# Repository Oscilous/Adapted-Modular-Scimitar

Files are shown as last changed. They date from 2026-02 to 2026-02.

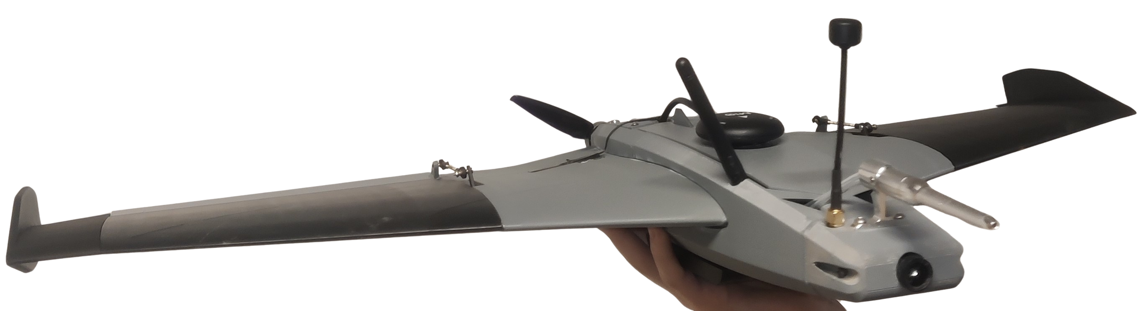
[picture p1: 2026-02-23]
Media/Assembly/4.png

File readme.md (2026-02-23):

# Adapted Modular Scimitar with Payload Mounting Grid

Repository of the HardwareX paper "Field-tested workflow for adapting open-source 3D-printed fixed-wing UAVs for modular payload integration" developed at University of Southern Denmark.



## Abstract

Fixed-wing unmanned aerial vehicles (UAVs) are widely used in environmental monitoring and research, yet sys-
tematic and reproducible methods for integrating arbitrary payloads while preserving aerodynamic performance
remain limited. This work presents a complete hardware workflow for adapting an open-source fixed-wing air-
frame into a modular sensing platform with validated payload integration. The approach combines mechanical
redesign, mass and center of gravity verification, computational fluid dynamics (CFD) aerodynamic assess-
ment, and field validation. The workflow is demonstrated on a sub-1.5 kg 3D-printed Scimitar V2 modified to
be equipped with a reconfigurable payload mounting grid that enables rapid sensor interchange. CFD-guided
design iteration increased aerodynamic efficiency by raising the lift-to-drag ratio from approximately 3.6–5.1
to 8.8–18.2, providing quantitative pre-fabrication screening indicating improved aerodynamic efficiency. Field
testing at RC Parken (Aabenraa, Denmark) in December 2025 validated the sensor logging pipeline by cross-
comparing barometric pressure and demonstrated in-flight temperature and humidity acquisition.

## Directory Structure

```
├── readme.md                    # This file
├── 3D_Printing/                 # 3D printable components
│   ├── 019_Canopy_handle.3mf
│   └── TPU/                     # Flexible TPU parts
│       └── 015_Hinges_TPU.3mf
├── CAD/                         # Complete CAD models (STEP format)
│   ├── Fuselage sections (001-007)
│   ├── Wing designs (008-013)
│   ├── Control surfaces (014-016)
│   ├── Canopy (017, 019)
│   ├── Sensor and component models (018, 020-035)
│   └── [35 STEP files total]
├── CFD/                         # Aerodynamic analysis files
│   ├── project_results.xml
│   ├── Internal_M5GO.*          # Simulation results
│   └── r_000000.fld             # Field data
├── M5 Software/                 # M5Stack firmware
│   └── Drone_Air_Quality_Code.m5f2
├── PX4 Firmware/                # Autopilot configuration
│   ├── Parameters.params        # Pre-tuned parameters
│   └── readme.txt
└── Media/                       # Assembly documentation
    └── Assembly/
```

## License

This project is released under CC BY 4.0.

For questions, contributions, or feedback, please refer to the project repository or contact the team.

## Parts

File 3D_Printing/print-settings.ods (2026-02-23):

For print orientation please navigate to docs/gallery/printing-orientation/
 | Scimitar 2
Part | Profile | Infill % | Time (P1P) | Grams | Modifiers
Wing L 1 | A | 4 gyro | 02:14 | 50 | +support
Wing R 1 | A | 4 gyro | 02:14 | 50 | +support
Wing L 2 | A | 4 gyro | 03:24 | 49 | +support
Wing R 2 | A | 4 gyro | 03:24 | 49 | +support
Wing L 3 | B LW | 8 gyro | 01:09 | 16
Wing R 3 | B LW | 8 gyro | 01:09 | 16
Wing L aileron | A | 8 gyro | 01:25 | 9 | 15 bottom layers
Wing R aileron | A | 8 gyro | 01:25 | 9 | 15 bottom layers
Fuselage 1 | C | 0 | 00:38 | 14
Fuselage 2 | C | 100 | 00:09 | 4
Fuselage 3 | A | 8 gyro | 03:07 | 43 | 10 bottom layers
Fuselage 4 | A | 8 gyro | 02:12 | 32
Fuselage 5 | C | 0 | 00:23 | 8
Batterie plate | C | 10 gyro | 00:20 | 12 | 3 bottom, 3 top
Canopy | C | 8 gyro | 00:28 | 14 | 2 bottom, 2 top
Canopy handle | B | 100 | 00:05 | 1
Motor mount | C | 100 | 00:24 | 6
Wing lock L+R | C | 100 | 00:31 | 15
Hinges (TPU) | B | 100 | 00:10 | 1
 | Total : |  | 24:51 | 398
Profile | Layer hei. | Walls | Top, bottom
A | 0,20 | 1 | 3 | PLA+
B | 0,20 | 2 | 4
C | 0,20 | 3 | 5
A LW | 0,2 | 1 | 3 | Esun / 3DLP Foaming PLA-LW 250°C flow 0.50
B LW | 0,2 | 2 | 4
C LW | 0,2 | 3 | 5

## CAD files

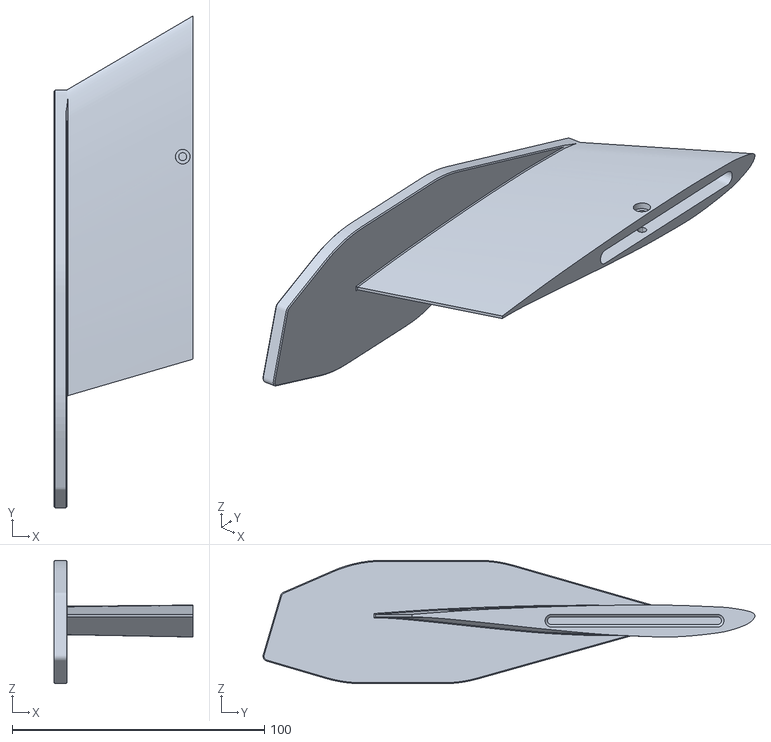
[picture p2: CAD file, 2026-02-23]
3D_Printing/LWPLA/013_Wing_3_Right.STL
55.0 x 195.2 x 49.0

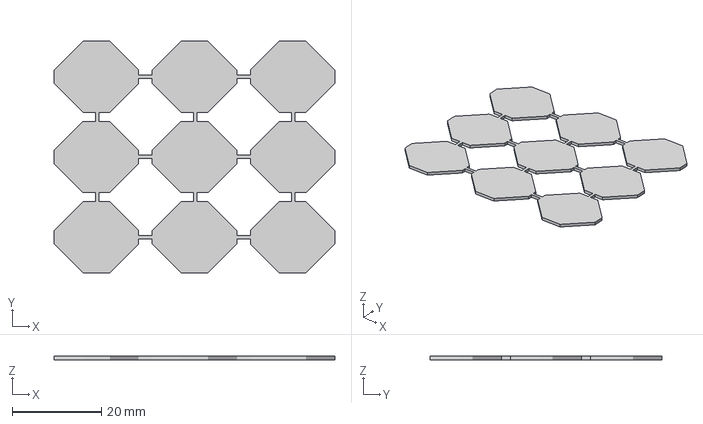
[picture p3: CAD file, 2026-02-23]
3D_Printing/TPU/015_Hinges_TPU.3mf
63.0 x 52.0 x 0.8 mm

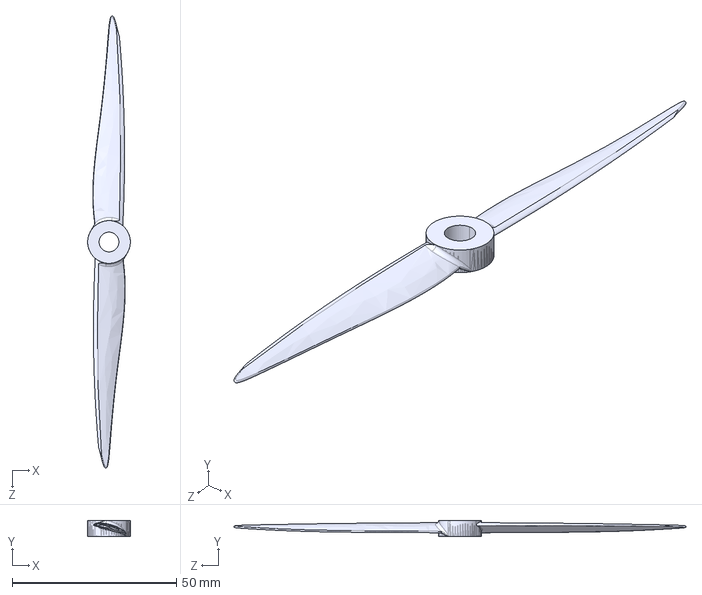
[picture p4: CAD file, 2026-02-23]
CAD/033_6042_propeller.STEP
13.0 x 5.00 x 137.4 mm

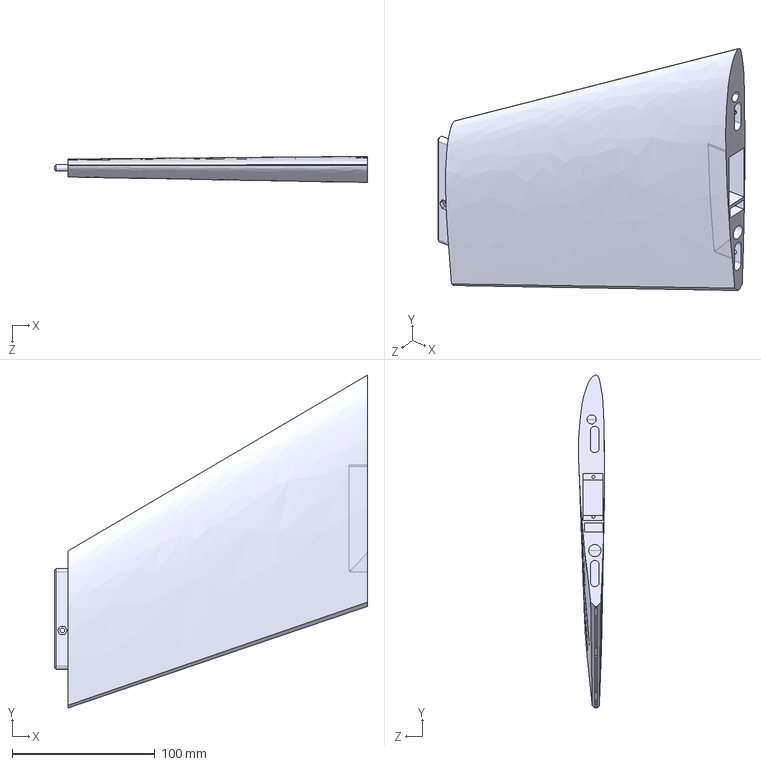
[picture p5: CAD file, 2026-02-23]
CAD/010_Wing_2_Left.STEP
219.6 x 233.5 x 18.4 mm

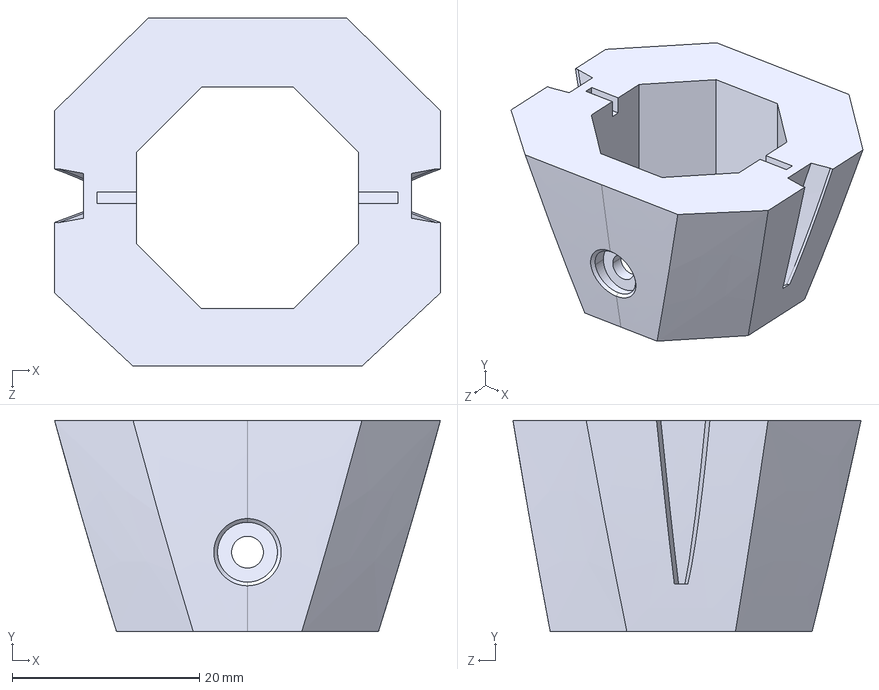
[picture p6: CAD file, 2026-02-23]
CAD/005_Fuselage_5.STEP
41.3 x 22.6 x 37.2 mm

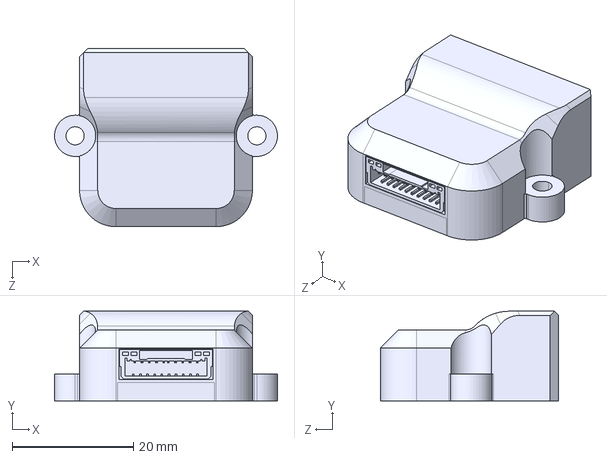
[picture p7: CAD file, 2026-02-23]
CAD/024_PWM_extention_module.STEP
36.8 x 14.8 x 29.4 mm

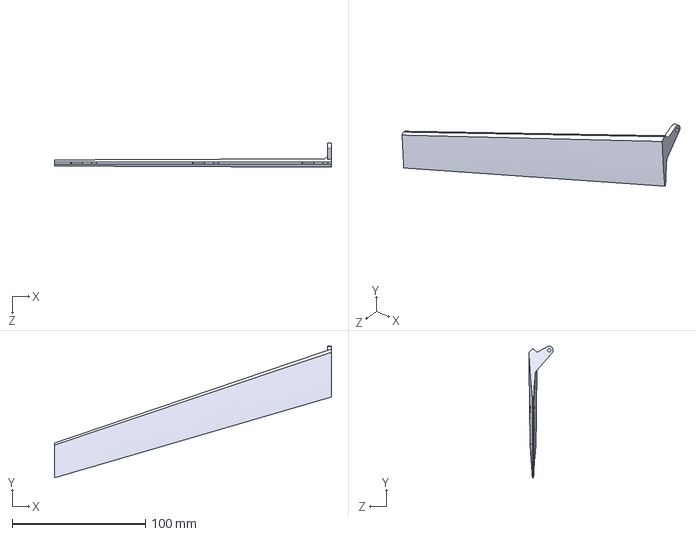
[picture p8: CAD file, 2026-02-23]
CAD/016_Aileron_Right.STEP
208.0 x 98.8 x 18.3 mm

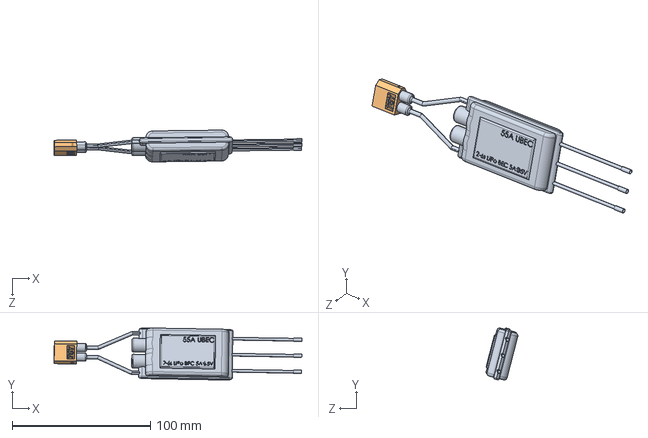
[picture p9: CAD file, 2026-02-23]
CAD/025_ubec.STEP
179.5 x 37.6 x 23.0 mm
UBEC
XT-60_female

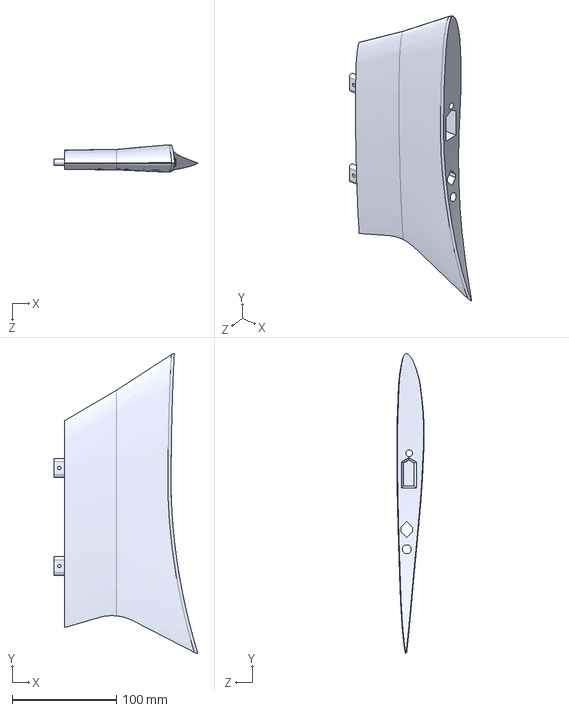
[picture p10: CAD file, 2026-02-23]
CAD/009_Wing_1_Right.STEP
137.9 x 287.6 x 26.3 mm

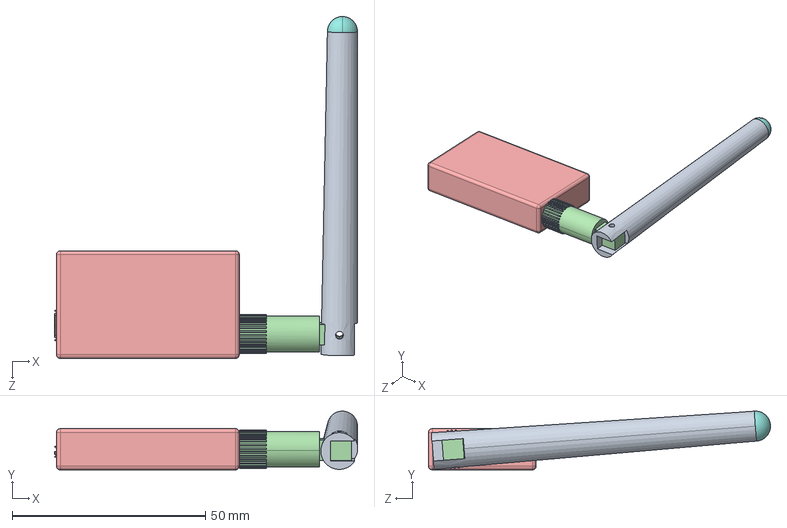
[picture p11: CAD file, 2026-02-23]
CAD/022_Telemetry_Holybro.STEP
78.6 x 15.2 x 88.6 mm

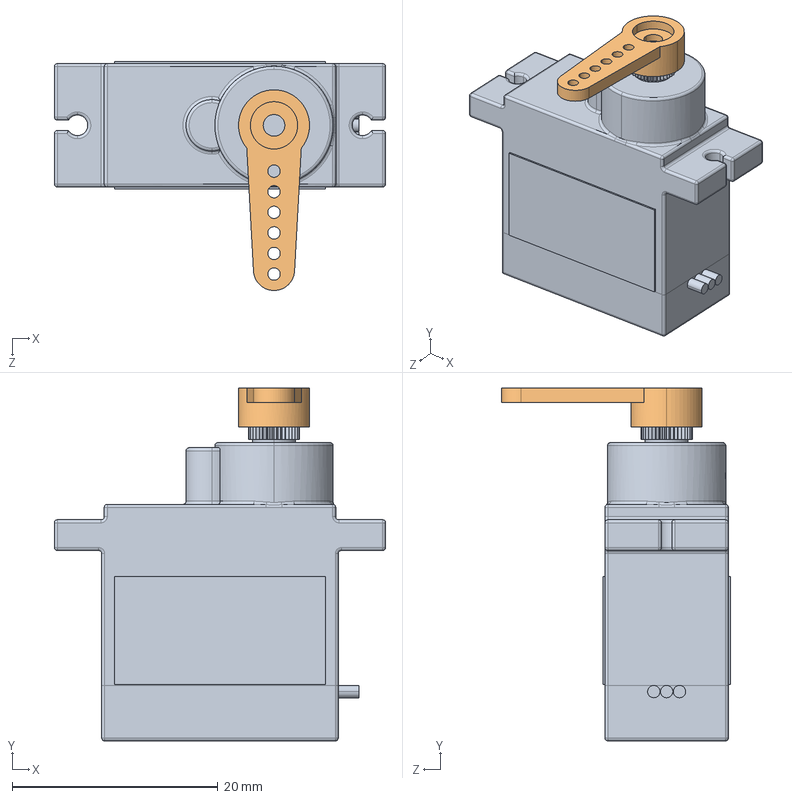
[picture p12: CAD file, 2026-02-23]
CAD/031_Left_wing_Servo_MG90S.STEP
32.2 x 34.3 x 22.2 mm

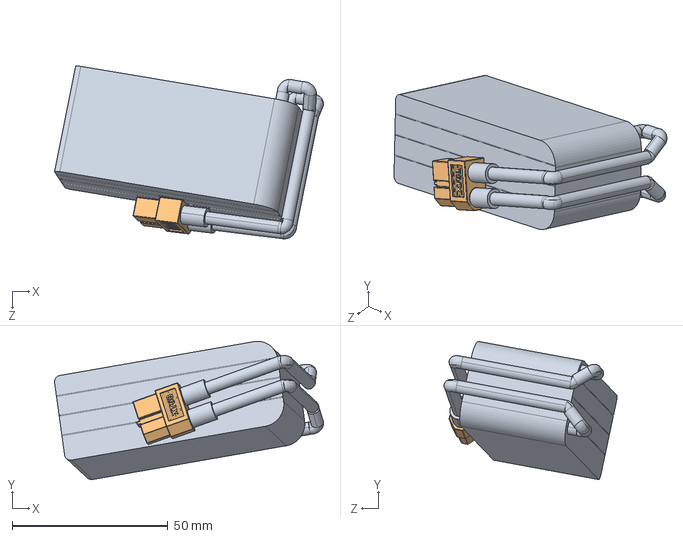
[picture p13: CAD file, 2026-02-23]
CAD/021_Battery_Tattu.STEP
86.3 x 44.3 x 55.5 mm
tattu 1300mAh_4S
XT60 Buchse_Predeterminado

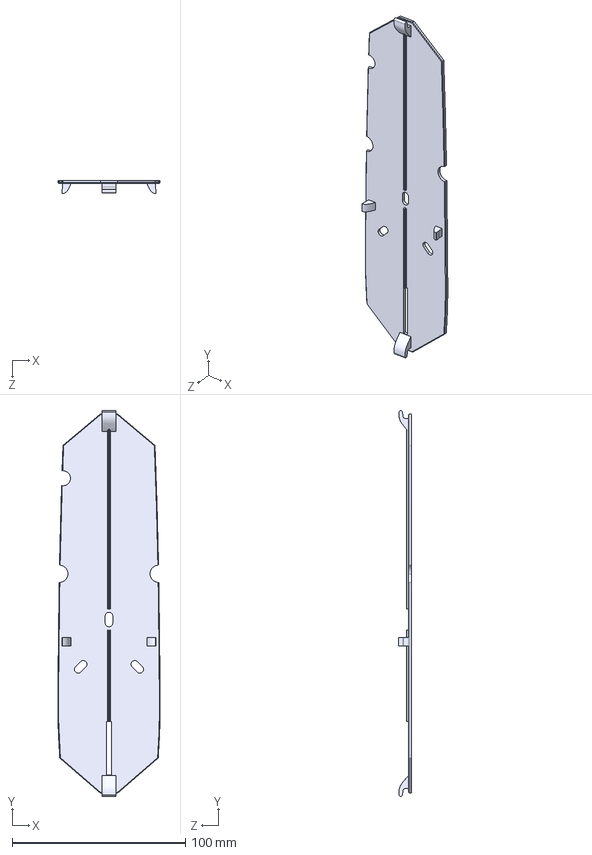
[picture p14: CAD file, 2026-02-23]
CAD/017_Canopy.STEP
59.2 x 222.9 x 7.74 mm

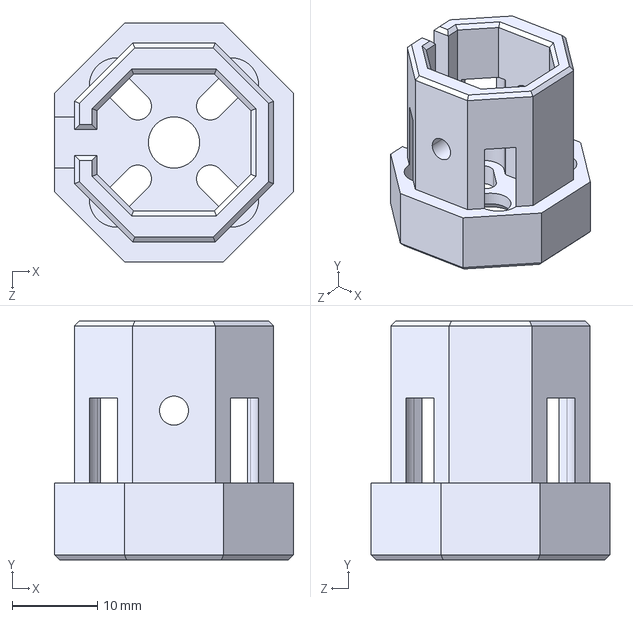
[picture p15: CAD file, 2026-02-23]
CAD/006_Fuselage_6.STEP
28.0 x 28.0 x 28.0 mm

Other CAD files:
3D_Printing/LWPLA/012_Wing_3_Left.STL
CAD/014_Aileron_Left.STEP
CAD/008_Wing_1_Left.STEP
CAD/013_Wing_3_Right.STEP
3D_Printing/001_Fuselage_1.STL
3D_Printing/002_Fuselage_2.STL
3D_Printing/003_Fuselage_3.STL
3D_Printing/004_Fuselage_4.STL
3D_Printing/005_Fuselage_5.STL
3D_Printing/006_Fuselage_6.STL
3D_Printing/007_Fuselage_4_lid.STL
3D_Printing/008_Wing_1_Left.STL
3D_Printing/009_Wing_1_Right.STL
3D_Printing/010_Wing_2_Left.STL
3D_Printing/011_Wing_2_Right.STL
3D_Printing/014_Aileron_Left.STL
3D_Printing/016_Aileron_Right.STL
3D_Printing/017_Canopy.STL
3D_Printing/018_Sensor_Grid_.STL
3D_Printing/019_Canopy_handle.3mf
CAD/001_Fuselage_1.STEP
CAD/002_Fuselage_2.STEP
CAD/003_Fuselage_3.STEP
CAD/004_Fuselage_4.STEP
CAD/007_Fuselage_4_lid.STEP
CAD/011_Wing_2_Right.STEP
CAD/012_Wing_3_Left.STEP
CAD/015_Hinges.STEP
CAD/018_Sensor_Grid.STEP
CAD/019_Canopy_handle.STEP
CAD/020_Holybro_PT60.STEP
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

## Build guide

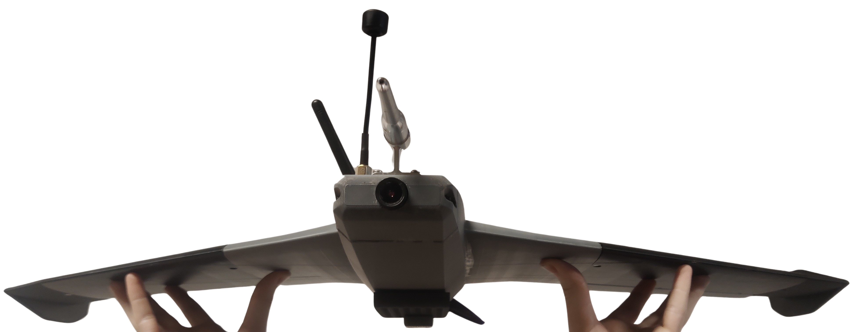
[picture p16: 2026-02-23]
Media/Assembly/3.png

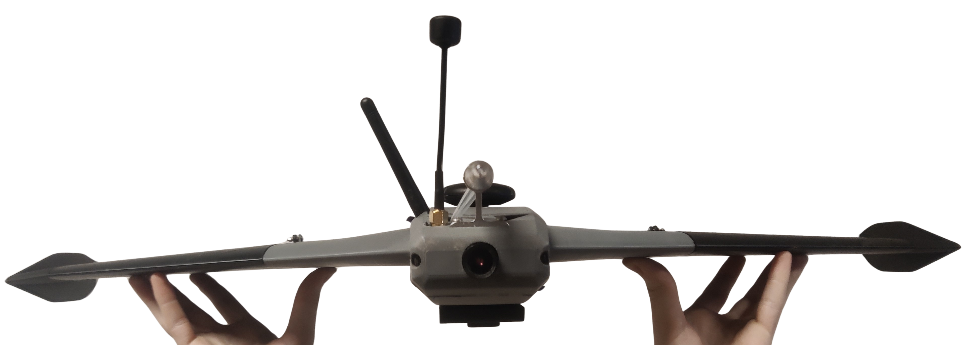
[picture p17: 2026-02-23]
Media/Assembly/2.png

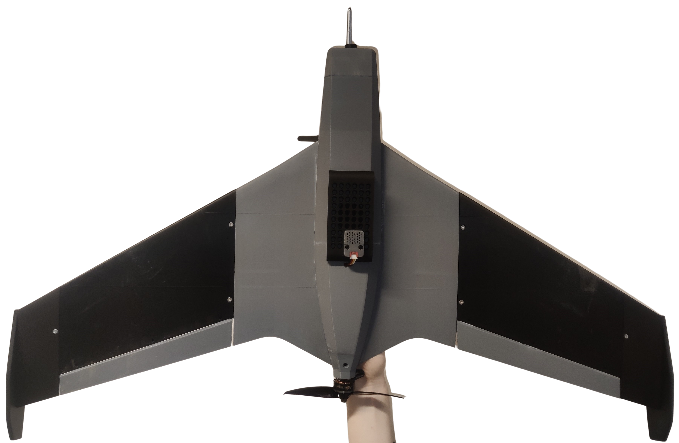
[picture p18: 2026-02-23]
Media/Assembly/5.png

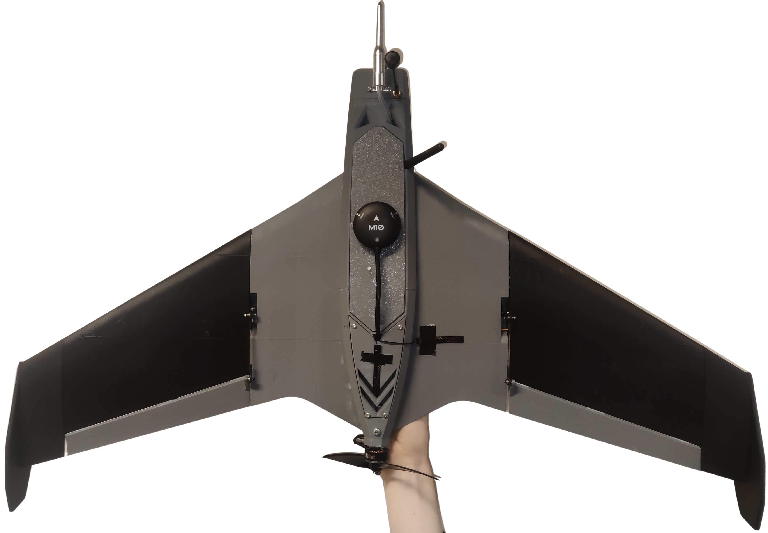
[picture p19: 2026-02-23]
Media/Assembly/1.png

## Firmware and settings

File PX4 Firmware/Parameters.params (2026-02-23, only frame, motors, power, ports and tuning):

1	1	BAT1_A_PER_V	2977.475341796875000000	9
1	1	BAT1_CAPACITY	-1.000000000000000000	9
1	1	BAT1_I_CHANNEL	-1	6
1	1	BAT1_I_OVERWRITE	0.000000000000000000	9
1	1	BAT1_N_CELLS	4	6
1	1	BAT1_R_INTERNAL	0.004999999888241291	9
1	1	BAT1_SOURCE	0	6
1	1	BAT1_V_CHANNEL	-1	6
1	1	BAT1_V_CHARGED	4.199999809265136719	9
1	1	BAT1_V_DIV	18.259523391723632813	9
1	1	BAT1_V_EMPTY	3.599999904632568359	9
1	1	BAT2_A_PER_V	36.367515563964843750	9
1	1	BAT2_CAPACITY	-1.000000000000000000	9
1	1	BAT2_I_CHANNEL	-1	6
1	1	BAT2_I_OVERWRITE	0.000000000000000000	9
1	1	BAT2_N_CELLS	0	6
1	1	BAT2_R_INTERNAL	0.004999999888241291	9
1	1	BAT2_SOURCE	-1	6
1	1	BAT2_V_CHANNEL	-1	6
1	1	BAT2_V_CHARGED	4.050000190734863281	9
1	1	BAT2_V_DIV	18.100000381469726563	9
1	1	BAT2_V_EMPTY	3.599999904632568359	9
1	1	BAT_AVRG_CURRENT	15.000000000000000000	9
1	1	BAT_CRIT_THR	0.070000000298023224	9
1	1	BAT_EMERGEN_THR	0.050000000745058060	9
1	1	BAT_LOW_THR	0.150000005960464478	9
1	1	BAT_V_OFFS_CURR	0.000000000000000000	9
1	1	CA_AIRFRAME	1	6
1	1	CA_ROTOR0_CT	6.500000000000000000	9
1	1	CA_ROTOR0_KM	0.050000000745058060	9
1	1	CA_ROTOR0_PX	0.150000005960464478	9
1	1	CA_ROTOR0_PY	0.000000000000000000	9
1	1	CA_ROTOR0_PZ	0.000000000000000000	9
1	1	CA_ROTOR10_CT	6.500000000000000000	9
1	1	CA_ROTOR10_KM	0.050000000745058060	9
1	1	CA_ROTOR10_PX	0.000000000000000000	9
1	1	CA_ROTOR10_PY	0.000000000000000000	9
1	1	CA_ROTOR10_PZ	0.000000000000000000	9
1	1	CA_ROTOR11_CT	6.500000000000000000	9
1	1	CA_ROTOR11_KM	0.050000000745058060	9
1	1	CA_ROTOR11_PX	0.000000000000000000	9
1	1	CA_ROTOR11_PY	0.000000000000000000	9
1	1	CA_ROTOR11_PZ	0.000000000000000000	9
1	1	CA_ROTOR1_CT	6.500000000000000000	9
1	1	CA_ROTOR1_KM	0.050000000745058060	9
1	1	CA_ROTOR1_PX	0.000000000000000000	9
1	1	CA_ROTOR1_PY	0.000000000000000000	9
1	1	CA_ROTOR1_PZ	0.000000000000000000	9
1	1	CA_ROTOR2_CT	6.500000000000000000	9
1	1	CA_ROTOR2_KM	0.050000000745058060	9
1	1	CA_ROTOR2_PX	0.000000000000000000	9
1	1	CA_ROTOR2_PY	0.000000000000000000	9
1	1	CA_ROTOR2_PZ	0.000000000000000000	9
1	1	CA_ROTOR3_CT	6.500000000000000000	9
1	1	CA_ROTOR3_KM	0.050000000745058060	9
1	1	CA_ROTOR3_PX	0.000000000000000000	9
1	1	CA_ROTOR3_PY	0.000000000000000000	9
1	1	CA_ROTOR3_PZ	0.000000000000000000	9
1	1	CA_ROTOR4_CT	6.500000000000000000	9
1	1	CA_ROTOR4_KM	0.050000000745058060	9
1	1	CA_ROTOR4_PX	0.000000000000000000	9
1	1	CA_ROTOR4_PY	0.000000000000000000	9
1	1	CA_ROTOR4_PZ	0.000000000000000000	9
1	1	CA_ROTOR5_CT	6.500000000000000000	9
1	1	CA_ROTOR5_KM	0.050000000745058060	9
1	1	CA_ROTOR5_PX	0.000000000000000000	9
1	1	CA_ROTOR5_PY	0.000000000000000000	9
1	1	CA_ROTOR5_PZ	0.000000000000000000	9
1	1	CA_ROTOR6_CT	6.500000000000000000	9
1	1	CA_ROTOR6_KM	0.050000000745058060	9
1	1	CA_ROTOR6_PX	0.000000000000000000	9
1	1	CA_ROTOR6_PY	0.000000000000000000	9
1	1	CA_ROTOR6_PZ	0.000000000000000000	9
1	1	CA_ROTOR7_CT	6.500000000000000000	9
1	1	CA_ROTOR7_KM	0.050000000745058060	9
1	1	CA_ROTOR7_PX	0.000000000000000000	9
1	1	CA_ROTOR7_PY	0.000000000000000000	9
1	1	CA_ROTOR7_PZ	0.000000000000000000	9
1	1	CA_ROTOR8_CT	6.500000000000000000	9
1	1	CA_ROTOR8_KM	0.050000000745058060	9
1	1	CA_ROTOR8_PX	0.000000000000000000	9
1	1	CA_ROTOR8_PY	0.000000000000000000	9
1	1	CA_ROTOR8_PZ	0.000000000000000000	9
1	1	CA_ROTOR9_CT	6.500000000000000000	9
1	1	CA_ROTOR9_KM	0.050000000745058060	9
1	1	CA_ROTOR9_PX	0.000000000000000000	9
1	1	CA_ROTOR9_PY	0.000000000000000000	9
1	1	CA_ROTOR9_PZ	0.000000000000000000	9
1	1	CA_ROTOR_COUNT	1	6
1	1	MOT_POLE_COUNT	14	6
1	1	PWM_MAIN_DIS1	1900	6
1	1	PWM_MAIN_DIS2	1500	6
1	1	PWM_MAIN_DIS3	1500	6
1	1	PWM_MAIN_DIS4	900	6
1	1	PWM_MAIN_DIS5	1500	6
1	1	PWM_MAIN_DIS6	1000	6
1	1	PWM_MAIN_DIS7	1000	6
1	1	PWM_MAIN_DIS8	1000	6
1	1	PWM_MAIN_FAIL1	-1	6
1	1	PWM_MAIN_FAIL2	-1	6
1	1	PWM_MAIN_FAIL3	-1	6
1	1	PWM_MAIN_FAIL4	-1	6
1	1	PWM_MAIN_FAIL5	-1	6
1	1	PWM_MAIN_FAIL6	-1	6
1	1	PWM_MAIN_FAIL7	-1	6
1	1	PWM_MAIN_FAIL8	-1	6
1	1	PWM_MAIN_FUNC1	0	6
1	1	PWM_MAIN_FUNC2	0	6
1	1	PWM_MAIN_FUNC3	0	6
1	1	PWM_MAIN_FUNC4	430	6
1	1	PWM_MAIN_FUNC5	0	6
1	1	PWM_MAIN_FUNC6	0	6
1	1	PWM_MAIN_FUNC7	0	6
1	1	PWM_MAIN_FUNC8	0	6
1	1	PWM_MAIN_MAX1	1900	6
1	1	PWM_MAIN_MAX2	2000	6
1	1	PWM_MAIN_MAX3	1900	6
1	1	PWM_MAIN_MAX4	1900	6
1	1	PWM_MAIN_MAX5	2000	6
1	1	PWM_MAIN_MAX6	2000	6
1	1	PWM_MAIN_MAX7	2000	6
1	1	PWM_MAIN_MAX8	2000	6
1	1	PWM_MAIN_MIN1	900	6
1	1	PWM_MAIN_MIN2	1000	6
1	1	PWM_MAIN_MIN3	1100	6
1	1	PWM_MAIN_MIN4	900	6
1	1	PWM_MAIN_MIN5	1000	6
1	1	PWM_MAIN_MIN6	1000	6
1	1	PWM_MAIN_MIN7	1000	6
1	1	PWM_MAIN_MIN8	1000	6
1	1	PWM_MAIN_TIM0	50	6
1	1	PWM_MAIN_TIM1	50	6
1	1	PWM_MAIN_TIM2	50	6
1	1	SYS_AUTOSTART	3000	6
